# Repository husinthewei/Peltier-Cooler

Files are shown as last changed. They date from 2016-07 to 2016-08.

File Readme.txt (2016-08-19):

Peltier Cooler Project

Main Programs:
*FLoop: 
	-Arduino program. Found within the "Arduino Programs" directory. 
	-Controls the Peltier's, monitors temperature, and communicates with the python script.
	-Loaded onto Arduino. Does not have to be uploaded every use.

*Com.py: 
	-Python Script. Found within the "Python Scripts" directory
	-Reads the temperature outputs from the Arduino, logs them in files, and emails if there is failure
	-Must be ran every use

How to run Com.py(NOTE: CURRENTLY ON WORKS ON WINDOWS):
  Requirements-
	*python:
	  There are many options to install python. There are tutorials for Windows if googled, or you could download Enthought Canopy.
	*pip:
	  Download http://www.pip-installer.org/en/latest/installing.html
	  In cmd, cd to the directory of the file downloaded and type: python get-pip.py
	*pyserial:
	  After pip is installed, type in cmd: python -m pip install pyserial
	*pyqtgraph
	  After pip is installed, type in cmd: python -m pip install pyqtgraph
  Procedure 1 (command line)-
	1. cd to the directory of the python script. Ex: cd C:\Users\Your_Username\Documents\Github\Peltier-Cooler\PythonScripts
	2. type: python -B Com.py
	3. Enter the com port. Ex: Usually type: 0 
	4. Enter how often you want data output

  Procedure 2 (user interface)-
	1. go to the Pelter-Cooler folder
	2. double click: RunPython
	3. Enter the com port. Ex: Usually type: 0 
	4. Enter how often you want data output

How to run FLoop:
  Requirements-
	*Arduino IDE:
	  https://www.arduino.cc/en/Main/Software
  Procedure-
	1. The Arduino program is likely already on the board. It automatically starts running when the Arduino is turned on.
	2. If not loaded on, run the Arduino IDE and open FLoop
	3. Click the upload button on the top left

Where to find data outputs: 
	- The data outputs are in a folder called "Logs" inside the PythonScripts directory
	- They are in the form of csv files and include a timestamp in their names. 
	
*NOTE: There are heavily commented versions of the programs left in the folders
*These may be used for better understanding of the programs
*However, they are likely obsolete and should not be run
*The other files/programs are either irrelevant or tests

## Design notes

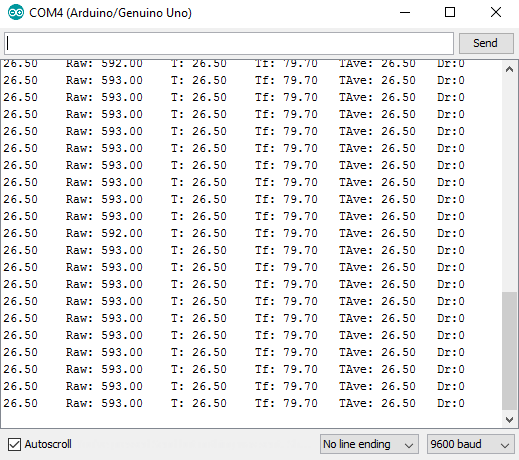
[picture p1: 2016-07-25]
PythonScripts/Images/arduinoOut.png

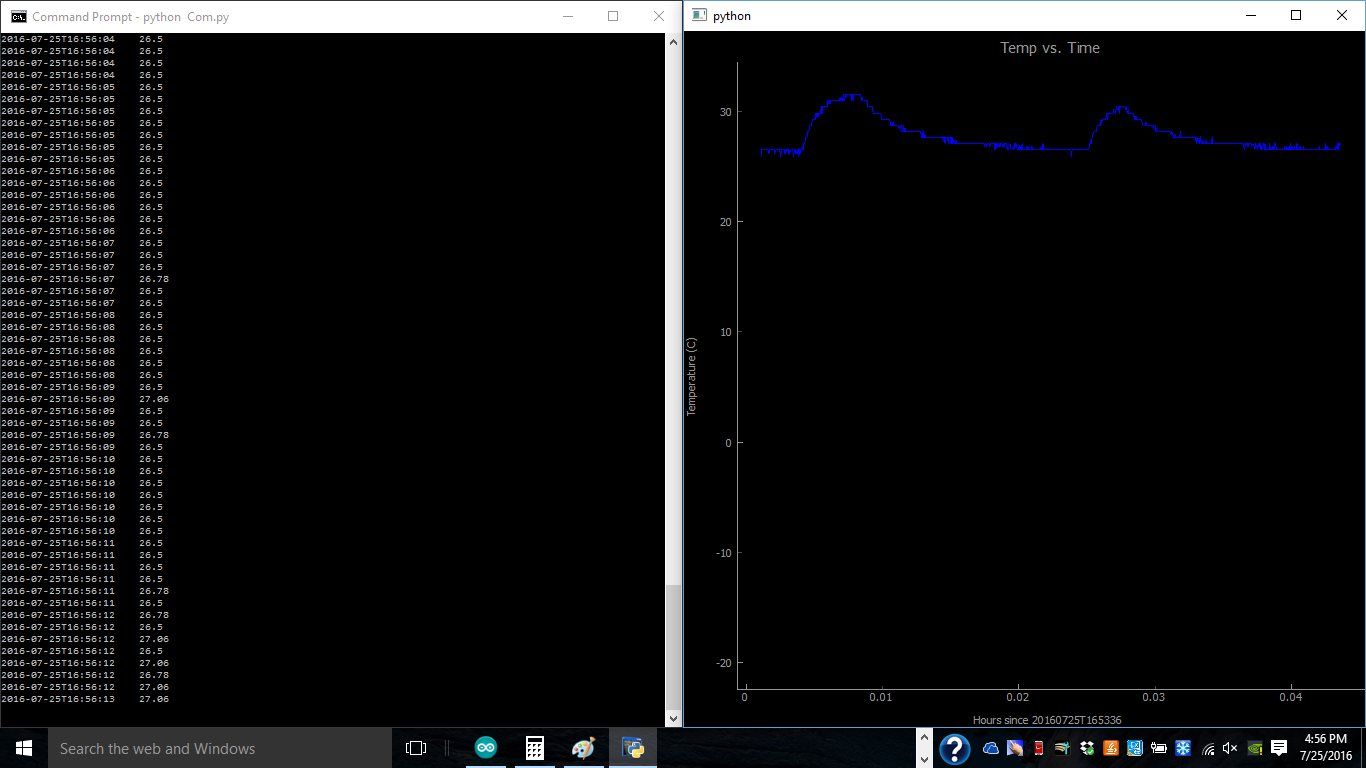
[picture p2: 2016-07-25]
PythonScripts/Images/GraphAndTerminal.png

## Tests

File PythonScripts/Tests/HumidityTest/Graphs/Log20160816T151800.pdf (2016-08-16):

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

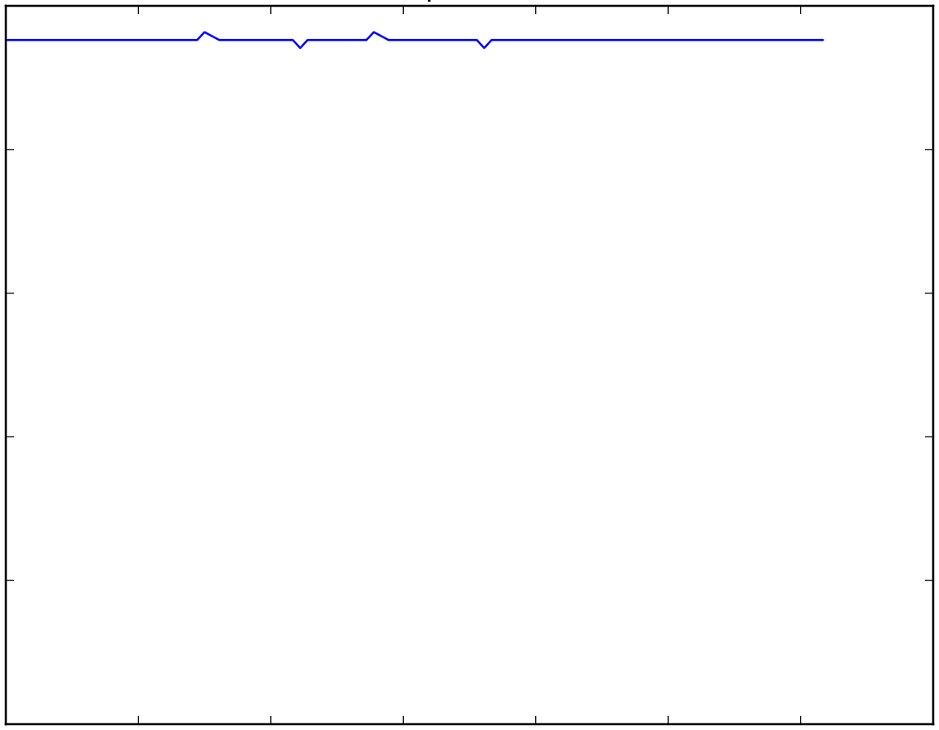
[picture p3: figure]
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

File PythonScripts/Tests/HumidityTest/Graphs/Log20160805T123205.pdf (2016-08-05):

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

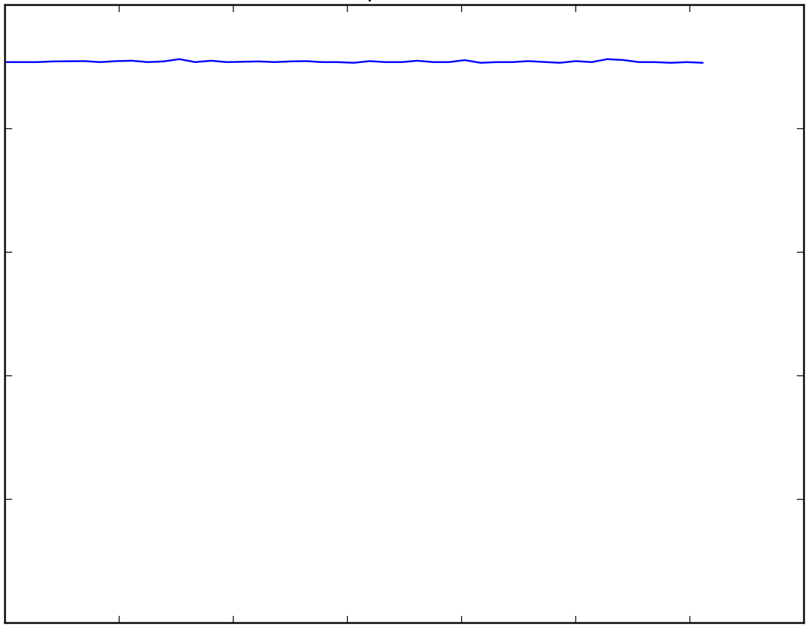
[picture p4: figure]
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

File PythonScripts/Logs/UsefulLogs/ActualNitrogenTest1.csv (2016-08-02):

2016-08-01T10:28:55 | -9.62905263158
2016-08-01T10:29:05 | -9.86350515464
2016-08-01T10:29:15 | -10.2303157895
2016-08-01T10:29:25 | -10.395106383
2016-08-01T10:29:36 | -10.7461702128
2016-08-01T10:29:46 | -10.9457446809
2016-08-01T10:29:56 | -11.1125531915
2016-08-01T10:30:06 | -11.4163829787
2016-08-01T10:30:16 | -11.5117021277
2016-08-01T10:30:26 | -11.5891489362
2016-08-01T10:30:36 | -11.7738297872
2016-08-01T10:30:46 | -11.9585106383
2016-08-01T10:30:56 | -12.0061702128
2016-08-01T10:31:06 | -12.0776595745
2016-08-01T10:31:16 | -12.2009473684
2016-08-01T10:31:26 | -12.3188421053
2016-08-01T10:31:36 | -12.4838947368
2016-08-01T10:31:46 | -12.5428421053
2016-08-01T10:31:56 | -12.5605263158
2016-08-01T10:32:06 | -12.6135789474
2016-08-01T10:32:16 | -12.6312631579
2016-08-01T10:32:26 | -12.6902105263
2016-08-01T10:32:36 | -12.7727368421
2016-08-01T10:32:46 | -12.8493684211
2016-08-01T10:32:56 | -12.8729473684
2016-08-01T10:33:06 | -12.8729473684
2016-08-01T10:33:16 | -13.0203157895
2016-08-01T10:33:26 | -13.1087368421
2016-08-01T10:33:36 | -13.15
2016-08-01T10:33:47 | -13.1323157895
2016-08-01T10:33:57 | -13.1558947368
2016-08-01T10:34:07 | -13.1912631579
2016-08-01T10:34:17 | -13.1971578947
2016-08-01T10:34:27 | -13.2266315789
2016-08-01T10:34:37 | -13.2914736842
2016-08-01T10:34:47 | -13.3091578947
2016-08-01T10:34:57 | -13.4034736842
2016-08-01T10:35:07 | -13.4801052632
2016-08-01T10:35:17 | -13.4683157895
2016-08-01T10:35:27 | -13.6213684211
2016-08-01T10:35:37 | -13.6274736842
2016-08-01T10:35:47 | -13.6745263158
2016-08-01T10:35:57 | -13.6509473684
2016-08-01T10:36:07 | -13.6628421053
2016-08-01T10:36:17 | -13.6391578947
2016-08-01T10:36:27 | -13.6510526316
2016-08-01T10:36:37 | -13.6982105263
2016-08-01T10:36:47 | -13.7272631579
2016-08-01T10:36:57 | -13.7038947368
2016-08-01T10:37:07 | -13.7211578947
2016-08-01T10:37:17 | -13.7036842105
2016-08-01T10:37:27 | -13.7094736842
2016-08-01T10:37:37 | -13.7210526316
2016-08-01T10:37:47 | -13.7272631579
2016-08-01T10:37:57 | -13.7561052632
2016-08-01T10:38:08 | -13.7736842105
2016-08-01T10:38:18 | -13.7910526316
2016-08-01T10:38:28 | -13.7968421053
2016-08-01T10:38:38 | -13.8025263158
2016-08-01T10:38:48 | -13.8316842105
2016-08-01T10:38:58 | -13.9185263158
2016-08-01T10:39:08 | -13.9243157895
2016-08-01T10:39:18 | -13.9414736842
2016-08-01T10:39:28 | -13.9994736842
2016-08-01T10:39:38 | -13.9937894737
2016-08-01T10:39:48 | -14.0458947368
2016-08-01T10:39:58 | -14.0051578947
2016-08-01T10:40:08 | -14.0109473684
2016-08-01T10:40:18 | -13.9937894737
2016-08-01T10:40:28 | -14.0515789474
2016-08-01T10:40:38 | -14.0401052632
2016-08-01T10:40:48 | -14.0918947368
2016-08-01T10:40:58 | -14.0921052632
2016-08-01T10:41:08 | -14.1327368421
2016-08-01T10:41:18 | -14.1498947368
2016-08-01T10:41:28 | -14.1329473684
2016-08-01T10:41:38 | -14.1327368421
2016-08-01T10:41:48 | -14.0747368421
2016-08-01T10:41:58 | -14.1212631579
2016-08-01T10:42:08 | -14.1152631579
2016-08-01T10:42:18 | -14.1501052632
2016-08-01T10:42:28 | -14.1796842105
2016-08-01T10:42:39 | -14.1616842105
2016-08-01T10:42:49 | -14.1672631579
2016-08-01T10:42:59 | -14.1326315789
2016-08-01T10:43:09 | -14.1849473684
2016-08-01T10:43:19 | -14.1731578947
2016-08-01T10:43:29 | -14.1554736842
2016-08-01T10:43:39 | -14.1441052632
2016-08-01T10:43:49 | -14.1968421053
2016-08-01T10:43:59 | -14.1443157895
2016-08-01T10:44:09 | -14.1906315789
2016-08-01T10:44:19 | -14.1674736842
2016-08-01T10:44:29 | -14.1965263158
2016-08-01T10:44:39 | -14.2255789474
2016-08-01T10:44:49 | -14.1791578947
2016-08-01T10:44:59 | -14.2083157895
2016-08-01T10:45:09 | -14.1675789474
2016-08-01T10:45:19 | -14.1556842105
2016-08-01T10:45:29 | -14.1615789474
2016-08-01T10:45:39 | -13.9529473684
2016-08-01T10:45:49 | -13.8314736842
2016-08-01T10:45:59 | -13.878
2016-08-01T10:46:09 | -13.9067368421
2016-08-01T10:46:19 | -14.0283157895
2016-08-01T10:46:29 | -14.0748421053
2016-08-01T10:46:39 | -14.0748421053
2016-08-01T10:46:49 | -14.1094736842
2016-08-01T10:47:00 | -14.1498947368
2016-08-01T10:47:10 | -14.1382105263
2016-08-01T10:47:20 | -14.1443157895
2016-08-01T10:47:30 | -14.2024210526
2016-08-01T10:47:40 | -14.1849473684
2016-08-01T10:47:50 | -14.1733684211
2016-08-01T10:48:00 | -14.2197894737
2016-08-01T10:48:10 | -14.1732631579
2016-08-01T10:48:20 | -14.2078947368
2016-08-01T10:48:30 | -14.2254736842
2016-08-01T10:48:40 | -14.2604210526
2016-08-01T10:48:50 | -14.2606315789
2016-08-01T10:49:00 | -14.2663157895
2016-08-01T10:49:10 | -14.2721052632
2016-08-01T10:49:20 | -14.2313684211
2016-08-01T10:49:30 | -14.2429473684
2016-08-01T10:49:40 | -14.2546315789
2016-08-01T10:49:50 | -14.2197894737
2016-08-01T10:50:00 | -14.2255789474
2016-08-01T10:50:10 | -14.2544210526
2016-08-01T10:50:20 | -14.272
2016-08-01T10:50:30 | -14.2837894737
2016-08-01T10:50:40 | -14.2663157895
2016-08-01T10:50:50 | -14.2662105263
2016-08-01T10:51:00 | -14.2605263158
2016-08-01T10:51:10 | -14.2428421053
2016-08-01T10:51:21 | -14.2781052632
2016-08-01T10:51:31 | -14.2428421053
2016-08-01T10:51:41 | -14.1849473684
2016-08-01T10:51:51 | -14.0630526316
2016-08-01T10:52:01 | -14.0575789474
2016-08-01T10:52:11 | -14.0344210526
2016-08-01T10:52:21 | -14.0922105263
2016-08-01T10:52:31 | -14.0746315789
2016-08-01T10:52:41 | -14.1269473684
2016-08-01T10:52:51 | -14.1269473684
2016-08-01T10:53:01 | -14.1384210526
2016-08-01T10:53:11 | -14.1616842105
2016-08-01T10:53:21 | -14.156
2016-08-01T10:53:31 | -14.1907368421
2016-08-01T10:53:41 | -14.1965263158
2016-08-01T10:53:51 | -14.2023157895
2016-08-01T10:54:01 | -14.1849473684
2016-08-01T10:54:11 | -14.1731578947
2016-08-01T10:54:21 | -14.1965263158
2016-08-01T10:54:31 | -14.1502105263
2016-08-01T10:54:41 | -14.1271578947
2016-08-01T10:54:51 | -14.1268421053
2016-08-01T10:55:01 | -14.1617894737
2016-08-01T10:55:11 | -14.1269473684
2016-08-01T10:55:21 | -14.1673684211
2016-08-01T10:55:31 | -14.1502105263
2016-08-01T10:55:41 | -14.2025263158
2016-08-01T10:55:52 | -14.2025263158
2016-08-01T10:56:02 | -14.2316842105
2016-08-01T10:56:12 | -14.1904210526
2016-08-01T10:56:22 | -14.2196842105
2016-08-01T10:56:32 | -14.1965263158
2016-08-01T10:56:42 | -14.2370526316
2016-08-01T10:56:52 | -14.2431578947
2016-08-01T10:57:02 | -14.1790526316
2016-08-01T10:57:12 | -14.2429473684
2016-08-01T10:57:22 | -14.2023157895
2016-08-01T10:57:32 | -14.2196842105
2016-08-01T10:57:42 | -14.1967368421
2016-08-01T10:57:52 | -14.208
2016-08-01T10:58:02 | -14.1674736842
2016-08-01T10:58:12 | -14.226
2016-08-01T10:58:22 | -14.2081052632
2016-08-01T10:58:32 | -14.2257894737
2016-08-01T10:58:42 | -14.2082105263
2016-08-01T10:58:52 | -14.1673684211
2016-08-01T10:59:02 | -14.1849473684
2016-08-01T10:59:12 | -14.1384210526
2016-08-01T10:59:22 | -14.0690526316
2016-08-01T10:59:32 | -13.8835789474
2016-08-01T10:59:42 | -13.8836842105
2016-08-01T10:59:52 | -13.93
2016-08-01T11:00:02 | -13.9009473684
2016-08-01T11:00:13 | -13.9706315789
2016-08-01T11:00:23 | -13.9704210526
2016-08-01T11:00:33 | -14.0285263158
2016-08-01T11:00:43 | -14.0226315789
2016-08-01T11:00:53 | -14.0053684211
2016-08-01T11:01:03 | -14.0401052632
2016-08-01T11:01:13 | -14.0631578947
2016-08-01T11:01:23 | -14.0807368421
2016-08-01T11:01:33 | -14.0867368421
2016-08-01T11:01:43 | -14.1211578947
2016-08-01T11:01:53 | -14.0981052632
2016-08-01T11:02:03 | -14.0341052632
2016-08-01T11:02:13 | -14.1096842105
2016-08-01T11:02:23 | -14.0976842105
2016-08-01T11:02:33 | -14.1498947368
2016-08-01T11:02:43 | -14.1269473684
2016-08-01T11:02:53 | -14.0982105263
2016-08-01T11:03:03 | -14.1502105263
2016-08-01T11:03:13 | -14.1384210526
2016-08-01T11:03:23 | -14.15
2016-08-01T11:03:33 | -14.1269473684
2016-08-01T11:03:43 | -14.1561052632
2016-08-01T11:03:53 | -14.1211578947
2016-08-01T11:04:03 | -14.1094736842
2016-08-01T11:04:13 | -14.1965263158
2016-08-01T11:04:23 | -14.15
2016-08-01T11:04:34 | -14.1672631579
2016-08-01T11:04:44 | -14.1615789474
2016-08-01T11:04:54 | -14.1675789474
2016-08-01T11:05:04 | -14.2024210526
2016-08-01T11:05:14 | -14.1675789474
2016-08-01T11:05:24 | -14.1907368421
2016-08-01T11:05:34 | -14.1790526316
2016-08-01T11:05:44 | -14.1443157895
2016-08-01T11:05:54 | -14.1445263158
2016-08-01T11:06:04 | -14.1733684211
2016-08-01T11:06:14 | -14.1734736842
2016-08-01T11:06:24 | -14.1848421053
2016-08-01T11:06:34 | -14.1963157895
2016-08-01T11:06:44 | -14.2315789474
2016-08-01T11:06:54 | -14.1730526316
2016-08-01T11:07:04 | -14.1963157895
2016-08-01T11:07:14 | -14.2021052632
2016-08-01T11:07:24 | -14.2255789474
2016-08-01T11:07:34 | -14.2372631579
2016-08-01T11:07:44 | -14.2196842105
2016-08-01T11:07:54 | -14.2254736842
2016-08-01T11:08:04 | -14.2082105263
2016-08-01T11:08:14 | -14.2372631579
2016-08-01T11:08:24 | -14.2431578947
2016-08-01T11:08:34 | -14.2137894737
2016-08-01T11:08:44 | -14.2195789474
2016-08-01T11:08:54 | -14.2371578947
2016-08-01T11:09:05 | -14.2548421053
2016-08-01T11:09:15 | -14.1907368421
2016-08-01T11:09:25 | -14.1213684211
2016-08-01T11:09:35 | -14.226
2016-08-01T11:09:45 | -14.1907368421
2016-08-01T11:09:55 | -14.2023157895
2016-08-01T11:10:05 | -14.208
2016-08-01T11:10:15 | -14.1675789474
2016-08-01T11:10:25 | -14.1617894737
2016-08-01T11:10:35 | -14.0224210526
2016-08-01T11:10:45 | -14.1093684211
2016-08-01T11:10:55 | -14.1905263158
2016-08-01T11:11:05 | -14.1616842105
2016-08-01T11:11:15 | -14.2605263158
2016-08-01T11:11:25 | -14.2256842105
2016-08-01T11:11:35 | -14.2430526316
2016-08-01T11:11:45 | -14.2255789474
2016-08-01T11:11:55 | -14.2372631579
2016-08-01T11:12:05 | -14.2490526316
2016-08-01T11:12:15 | -14.2606315789
2016-08-01T11:12:25 | -14.2313684211
2016-08-01T11:12:35 | -14.2314736842
2016-08-01T11:12:45 | -14.2661052632
2016-08-01T11:12:55 | -14.2662105263
2016-08-01T11:13:05 | -14.2136842105
2016-08-01T11:13:15 | -14.2549473684
2016-08-01T11:13:26 | -14.2197894737
2016-08-01T11:13:36 | -14.2312631579
2016-08-01T11:13:46 | -14.1964210526
2016-08-01T11:13:56 | -14.1851578947
2016-08-01T11:14:06 | -14.1789473684
2016-08-01T11:14:16 | -14.1966315789
2016-08-01T11:14:26 | -14.2254736842
2016-08-01T11:14:36 | -14.2313684211
2016-08-01T11:14:46 | -14.22
2016-08-01T11:14:56 | -14.1906315789
2016-08-01T11:15:06 | -14.2661052632
2016-08-01T11:15:16 | -14.214
2016-08-01T11:15:26 | -14.2022105263
2016-08-01T11:15:36 | -14.2024210526
2016-08-01T11:15:46 | -14.1963157895
2016-08-01T11:15:56 | -14.2195789474
2016-08-01T11:16:06 | -14.2198947368
2016-08-01T11:16:16 | -14.2313684211
2016-08-01T11:16:26 | -14.2428421053
2016-08-01T11:16:36 | -14.2724210526
2016-08-01T11:16:46 | -14.2257894737
2016-08-01T11:16:56 | -14.2312631579
2016-08-01T11:17:06 | -14.2314736842
2016-08-01T11:17:16 | -14.2313684211
2016-08-01T11:17:26 | -14.2082105263
2016-08-01T11:17:36 | -14.2430526316
2016-08-01T11:17:47 | -14.2081052632
2016-08-01T11:17:57 | -14.1673684211
2016-08-01T11:18:07 | -14.2428421053
2016-08-01T11:18:17 | -14.1847368421
2016-08-01T11:18:27 | -14.2083157895
2016-08-01T11:18:37 | -14.2723157895
2016-08-01T11:18:47 | -14.208
2016-08-01T11:18:57 | -14.2429473684
2016-08-01T11:19:07 | -14.2311578947
2016-08-01T11:19:17 | -14.2371578947
2016-08-01T11:19:27 | -14.3076842105
2016-08-01T11:19:37 | -14.2604210526
2016-08-01T11:19:47 | -14.2254736842
2016-08-01T11:19:57 | -14.2371578947
2016-08-01T11:20:07 | -14.2431578947
2016-08-01T11:20:17 | -14.2549473684
2016-08-01T11:20:27 | -14.2257894737
2016-08-01T11:20:37 | -14.22
2016-08-01T11:20:47 | -14.2489473684
2016-08-01T11:20:57 | -14.2314736842
2016-08-01T11:21:07 | -14.2314736842
2016-08-01T11:21:17 | -14.214
2016-08-01T11:21:27 | -14.2369473684
2016-08-01T11:21:37 | -14.2137894737
2016-08-01T11:21:47 | -14.2431578947
2016-08-01T11:21:57 | -14.2255789474
2016-08-01T11:22:07 | -14.2315789474
2016-08-01T11:22:18 | -14.2194736842
2016-08-01T11:22:28 | -14.2082105263
2016-08-01T11:22:38 | -14.2486315789
2016-08-01T11:22:48 | -14.2901052632
2016-08-01T11:22:58 | -14.2487368421
2016-08-01T11:23:08 | -14.2842105263
2016-08-01T11:23:18 | -14.2896842105
2016-08-01T11:23:28 | -14.2837894737
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

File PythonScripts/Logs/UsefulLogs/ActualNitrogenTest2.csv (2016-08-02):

2016-08-01T14:31:42 | 26.0692307692
2016-08-01T14:31:52 | 26.0092783505
2016-08-01T14:32:03 | 26.0092783505
2016-08-01T14:32:13 | 24.0405154639
2016-08-01T14:32:23 | 17.8235051546
2016-08-01T14:32:33 | 11.6530927835
2016-08-01T14:32:43 | 7.15367346939
2016-08-01T14:32:53 | 3.84326530612
2016-08-01T14:33:03 | 1.46153061224
2016-08-01T14:33:13 | -0.165360824742
2016-08-01T14:33:23 | -1.46041237113
2016-08-01T14:33:33 | -2.55731958763
2016-08-01T14:33:43 | -3.43453608247
2016-08-01T14:33:53 | -4.19278350515
2016-08-01T14:34:03 | -4.85659793814
2016-08-01T14:34:13 | -5.43969072165
2016-08-01T14:34:23 | -5.97659793814
2016-08-01T14:34:33 | -6.45
2016-08-01T14:34:43 | -6.80216494845
2016-08-01T14:34:53 | -7.12896907216
2016-08-01T14:35:04 | -7.50958762887
2016-08-01T14:35:14 | -7.66422680412
2016-08-01T14:35:24 | -7.94103092784
2016-08-01T14:35:34 | -7.99886597938
2016-08-01T14:35:44 | -8.18927835052
2016-08-01T14:35:54 | -8.40865979381
2016-08-01T14:36:04 | -8.63381443299
2016-08-01T14:36:14 | -8.72041237113
2016-08-01T14:36:24 | -8.83010309278
2016-08-01T14:36:34 | -8.98597938144
2016-08-01T14:36:44 | -9.18216494845
2016-08-01T14:36:54 | -9.28618556701
2016-08-01T14:37:04 | -9.40742268041
2016-08-01T14:37:14 | -9.44206185567
2016-08-01T14:37:24 | -9.48824742268
2016-08-01T14:37:34 | -9.47670103093
2016-08-01T14:37:44 | -9.50556701031
2016-08-01T14:37:54 | -9.44206185567
2016-08-01T14:38:04 | -9.45360824742
2016-08-01T14:38:14 | -9.37855670103
2016-08-01T14:38:24 | -9.25731958763
2016-08-01T14:38:35 | -9.17649484536
2016-08-01T14:38:45 | -9.17639175258
2016-08-01T14:38:55 | -9.17072164948
2016-08-01T14:39:05 | -9.17072164948
2016-08-01T14:39:15 | -9.16494845361
2016-08-01T14:39:25 | -9.20525773196
2016-08-01T14:39:35 | -9.21113402062
2016-08-01T14:39:45 | -9.25154639175
2016-08-01T14:39:55 | -9.32082474227
2016-08-01T14:40:05 | -9.3381443299
2016-08-01T14:40:15 | -9.35546391753
2016-08-01T14:40:25 | -9.37855670103
2016-08-01T14:40:35 | -9.39577319588
2016-08-01T14:40:45 | -9.3612371134
2016-08-01T14:40:55 | -9.42474226804
2016-08-01T14:41:05 | -9.43628865979
2016-08-01T14:41:15 | -9.44206185567
2016-08-01T14:41:25 | -9.41896907216
2016-08-01T14:41:35 | -9.37855670103
2016-08-01T14:41:45 | -9.49402061856
2016-08-01T14:41:56 | -9.44206185567
2016-08-01T14:42:06 | -9.52865979381
2016-08-01T14:42:16 | -9.61525773196
2016-08-01T14:42:26 | -9.67865979381
2016-08-01T14:42:36 | -9.7075257732
2016-08-01T14:42:46 | -9.74804123711
2016-08-01T14:42:56 | -9.74226804124
2016-08-01T14:43:06 | -9.77690721649
2016-08-01T14:43:16 | -9.73072164948
2016-08-01T14:43:26 | -9.7824742268
2016-08-01T14:43:36 | -9.74226804124
2016-08-01T14:43:46 | -9.75958762887
2016-08-01T14:43:56 | -9.80577319588
2016-08-01T14:44:06 | -9.75381443299
2016-08-01T14:44:16 | -9.80556701031
2016-08-01T14:44:26 | -9.84608247423
2016-08-01T14:44:36 | -9.78257731959
2016-08-01T14:44:46 | -9.8287628866
2016-08-01T14:44:57 | -9.83463917526
2016-08-01T14:45:07 | -9.89804123711
2016-08-01T14:45:17 | -9.87484536082
2016-08-01T14:45:27 | -9.90969072165
2016-08-01T14:45:37 | -9.88639175258
2016-08-01T14:45:47 | -9.95145833333
2016-08-01T14:45:57 | -9.90489583333
2016-08-01T14:46:07 | -9.9340625
2016-08-01T14:46:17 | -9.86340206186
2016-08-01T14:46:27 | -9.92229166667
2016-08-01T14:46:37 | -9.92822916667
2016-08-01T14:46:47 | -9.905
2016-08-01T14:46:57 | -9.9340625
2016-08-01T14:47:07 | -9.92802083333
2016-08-01T14:47:17 | -9.87505154639
2016-08-01T14:47:27 | -9.81154639175
2016-08-01T14:47:37 | -9.82309278351
2016-08-01T14:47:47 | -9.8518556701
2016-08-01T14:47:57 | -9.83463917526
2016-08-01T14:48:07 | -9.91072916667
2016-08-01T14:48:18 | -9.88639175258
2016-08-01T14:48:28 | -9.9212371134
2016-08-01T14:48:38 | -9.9340625
2016-08-01T14:48:48 | -9.96895833333
2016-08-01T14:48:58 | -10.0041666667
2016-08-01T14:49:08 | -9.98666666667
2016-08-01T14:49:18 | -9.98083333333
2016-08-01T14:49:28 | -10.0215625
2016-08-01T14:49:38 | -10.0332291667
2016-08-01T14:49:48 | -10.0768421053
2016-08-01T14:49:58 | -10.0040625
2016-08-01T14:50:08 | -10.0157291667
2016-08-01T14:50:18 | -10.0298947368
2016-08-01T14:50:28 | -10.0391666667
2016-08-01T14:50:38 | -10.1475789474
2016-08-01T14:50:48 | -10.1536842105
2016-08-01T14:50:58 | -10.1418947368
2016-08-01T14:51:09 | -10.2184210526
2016-08-01T14:51:19 | -10.2244210526
2016-08-01T14:51:29 | -10.3062765957
2016-08-01T14:51:39 | -10.330106383
2016-08-01T14:51:49 | -10.3181914894
2016-08-01T14:51:59 | -10.330106383
2016-08-01T14:52:09 | -10.329787234
2016-08-01T14:52:19 | -10.2947368421
2016-08-01T14:52:29 | -10.3179787234
2016-08-01T14:52:39 | -10.3179787234
2016-08-01T14:52:49 | -10.3654255319
2016-08-01T14:52:59 | -10.3479787234
2016-08-01T14:53:09 | -10.2948421053
2016-08-01T14:53:19 | -10.1769473684
2016-08-01T14:53:29 | -10.1653684211
2016-08-01T14:53:39 | -10.2596842105
2016-08-01T14:53:49 | -10.2822340426
2016-08-01T14:53:59 | -10.2714736842
2016-08-01T14:54:09 | -10.3121276596
2016-08-01T14:54:19 | -10.3180851064
2016-08-01T14:54:29 | -10.3061702128
2016-08-01T14:54:39 | -10.330106383
2016-08-01T14:54:49 | -10.3594680851
2016-08-01T14:54:59 | -10.3594680851
2016-08-01T14:55:09 | -10.394893617
2016-08-01T14:55:19 | -10.3594680851
2016-08-01T14:55:29 | -10.3657446809
2016-08-01T14:55:40 | -10.3654255319
2016-08-01T14:55:50 | -10.3420212766
2016-08-01T14:56:00 | -10.3653191489
2016-08-01T14:56:10 | -10.3061702128
2016-08-01T14:56:20 | -10.3121276596
2016-08-01T14:56:30 | -10.3358510638
2016-08-01T14:56:40 | -10.3064210526
2016-08-01T14:56:50 | -10.3240425532
2016-08-01T14:57:00 | -10.3180851064
2016-08-01T14:57:10 | -10.2949473684
2016-08-01T14:57:20 | -10.2891578947
2016-08-01T14:57:30 | -10.2942553191
2016-08-01T14:57:40 | -10.33
2016-08-01T14:57:50 | -10.2302105263
2016-08-01T14:58:00 | -10.2417894737
2016-08-01T14:58:10 | -10.2593684211
2016-08-01T14:58:20 | -10.2596842105
2016-08-01T14:58:30 | -10.3180851064
2016-08-01T14:58:40 | -10.2417894737
2016-08-01T14:58:50 | -10.3179787234
2016-08-01T14:59:01 | -10.2361052632
2016-08-01T14:59:11 | -10.1948421053
2016-08-01T14:59:21 | -10.2066315789
2016-08-01T14:59:31 | -10.2537894737
2016-08-01T14:59:41 | -10.2477894737
2016-08-01T14:59:51 | -10.2537894737
2016-08-01T15:00:01 | -10.2477894737
2016-08-01T15:00:11 | -10.2477894737
2016-08-01T15:00:21 | -10.33
2016-08-01T15:00:31 | -10.2882978723
2016-08-01T15:00:41 | -10.300212766
2016-08-01T15:00:51 | -10.3241489362
2016-08-01T15:01:01 | -10.2941489362
2016-08-01T15:01:11 | -10.3121276596
2016-08-01T15:01:21 | -10.3122340426
2016-08-01T15:01:31 | -10.3179787234
2016-08-01T15:01:41 | -10.2714736842
2016-08-01T15:01:51 | -10.2646808511
2016-08-01T15:02:01 | -10.2771578947
2016-08-01T15:02:12 | -10.2596842105
2016-08-01T15:02:22 | -10.2597894737
2016-08-01T15:02:32 | -10.2830526316
2016-08-01T15:02:42 | -10.329787234
2016-08-01T15:02:52 | -10.2890526316
2016-08-01T15:03:02 | -10.2706382979
2016-08-01T15:03:12 | -10.3237234043
2016-08-01T15:03:22 | -10.3654255319
2016-08-01T15:03:32 | -10.4713829787
2016-08-01T15:03:42 | -10.5763829787
2016-08-01T15:03:52 | -10.8280851064
2016-08-01T15:04:02 | -10.9756382979
2016-08-01T15:04:12 | -11.3272340426
2016-08-01T15:04:22 | -11.4880851064
2016-08-01T15:04:32 | -11.6428723404
2016-08-01T15:04:42 | -11.9763829787
2016-08-01T15:04:52 | -12.000212766
2016-08-01T15:05:02 | -11.9824468085
2016-08-01T15:05:12 | -11.5831914894
2016-08-01T15:05:22 | -12.0359574468
2016-08-01T15:05:32 | -12.2363157895
2016-08-01T15:05:42 | -12.4309473684
2016-08-01T15:05:52 | -12.3836842105
2016-08-01T15:06:03 | -12.4662105263
2016-08-01T15:06:13 | -12.5487368421
2016-08-01T15:06:23 | -12.6076842105
2016-08-01T15:06:33 | -12.5958947368
2016-08-01T15:06:43 | -12.6430526316
2016-08-01T15:06:53 | -12.6666315789
2016-08-01T15:07:03 | -12.6842105263
2016-08-01T15:07:13 | -12.7786315789
2016-08-01T15:07:23 | -12.7491578947
2016-08-01T15:07:33 | -12.8670526316
2016-08-01T15:07:43 | -12.9317894737
2016-08-01T15:07:53 | -12.9613684211
2016-08-01T15:08:03 | -13.0026315789
2016-08-01T15:08:13 | -13.0497894737
2016-08-01T15:08:23 | -13.0556842105
2016-08-01T15:08:33 | -13.1205263158
2016-08-01T15:08:43 | -13.1204210526
2016-08-01T15:08:53 | -13.1087368421
2016-08-01T15:09:03 | -13.1675789474
2016-08-01T15:09:13 | -13.1323157895
2016-08-01T15:09:23 | -13.2028421053
2016-08-01T15:09:33 | -13.1558947368
2016-08-01T15:09:43 | -13.1382105263
2016-08-01T15:09:53 | -13.15
2016-08-01T15:10:04 | -13.1441052632
2016-08-01T15:10:14 | -13.1615789474
2016-08-01T15:10:24 | -13.1790526316
2016-08-01T15:10:34 | -13.1498947368
2016-08-01T15:10:44 | -13.1558947368
2016-08-01T15:10:54 | -13.1264210526
2016-08-01T15:11:04 | -13.0674736842
2016-08-01T15:11:14 | -13.0262105263
2016-08-01T15:11:24 | -13.1026315789
2016-08-01T15:11:34 | -13.1027368421
2016-08-01T15:11:44 | -13.1616842105
2016-08-01T15:11:54 | -13.1382105263
2016-08-01T15:12:04 | -13.144
2016-08-01T15:12:14 | -13.1676842105
2016-08-01T15:12:24 | -13.1912631579
2016-08-01T15:12:34 | -13.2382105263
2016-08-01T15:12:44 | -13.1970526316
2016-08-01T15:12:54 | -13.2205263158
2016-08-01T15:13:04 | -13.2736842105
2016-08-01T15:13:14 | -13.2442105263
2016-08-01T15:13:24 | -13.2383157895
2016-08-01T15:13:34 | -13.2973684211
2016-08-01T15:13:44 | -13.2618947368
2016-08-01T15:13:54 | -13.3148421053
2016-08-01T15:14:04 | -13.3444210526
2016-08-01T15:14:14 | -13.3854736842
2016-08-01T15:14:25 | -13.368
2016-08-01T15:14:35 | -13.4150526316
2016-08-01T15:14:45 | -13.3504210526
2016-08-01T15:14:55 | -13.3504210526
2016-08-01T15:15:05 | -13.3443157895
2016-08-01T15:15:15 | -13.3798947368
2016-08-01T15:15:25 | -13.3267368421
2016-08-01T15:15:35 | -13.3738947368
2016-08-01T15:15:45 | -13.4034736842
2016-08-01T15:15:55 | -13.3268421053
2016-08-01T15:16:05 | -13.3973684211
2016-08-01T15:16:15 | -13.362
2016-08-01T15:16:25 | -13.4092631579
2016-08-01T15:16:35 | -13.4564210526
2016-08-01T15:16:45 | -13.4327368421
2016-08-01T15:16:55 | -13.4561052632
2016-08-01T15:17:05 | -13.4446315789
2016-08-01T15:17:15 | -13.4211578947
2016-08-01T15:17:25 | -13.4506315789
2016-08-01T15:17:35 | -13.4150526316
2016-08-01T15:17:45 | -13.4564210526
2016-08-01T15:17:55 | -13.5211578947
2016-08-01T15:18:05 | -13.5092631579
2016-08-01T15:18:15 | -13.4976842105
2016-08-01T15:18:25 | -13.4564210526
2016-08-01T15:18:35 | -13.4387368421
2016-08-01T15:18:46 | -13.4446315789
2016-08-01T15:18:56 | -13.5449473684
2016-08-01T15:19:06 | -13.4916842105
2016-08-01T15:19:16 | -13.5270526316
2016-08-01T15:19:26 | -13.5564210526
2016-08-01T15:19:36 | -13.4210526316
2016-08-01T15:19:46 | -13.4917894737
2016-08-01T15:19:56 | -13.486
2016-08-01T15:20:06 | -13.5271578947
2016-08-01T15:20:16 | -13.3916842105
2016-08-01T15:20:26 | -13.4447368421
2016-08-01T15:20:36 | -13.4502105263
2016-08-01T15:20:46 | -13.486
2016-08-01T15:20:56 | -13.4975789474
2016-08-01T15:21:06 | -13.5328421053
2016-08-01T15:21:16 | -13.6095789474
2016-08-01T15:21:26 | -13.5213684211
2016-08-01T15:21:36 | -13.5625263158
2016-08-01T15:21:46 | -13.5624210526
2016-08-01T15:21:56 | -13.5507368421
2016-08-01T15:22:06 | -13.5978947368
2016-08-01T15:22:16 | -13.5448421053
2016-08-01T15:22:26 | -13.6093684211
2016-08-01T15:22:36 | -13.6037894737
2016-08-01T15:22:46 | -13.5802105263
2016-08-01T15:22:56 | -13.598
2016-08-01T15:23:07 | -13.5684210526
2016-08-01T15:23:17 | -13.5331578947
2016-08-01T15:23:27 | -13.5272631579
2016-08-01T15:23:37 | -13.5682105263
2016-08-01T15:23:47 | -13.5861052632
2016-08-01T15:23:57 | -13.5975789474
2016-08-01T15:24:07 | -13.5449473684
2016-08-01T15:24:17 | -13.6272631579
2016-08-01T15:24:27 | -13.6332631579
2016-08-01T15:24:37 | -13.6391578947
2016-08-01T15:24:47 | -13.6155789474
2016-08-01T15:24:57 | -13.5802105263
2016-08-01T15:25:07 | -13.5978947368
2016-08-01T15:25:17 | -13.5803157895
2016-08-01T15:25:27 | -13.5862105263
2016-08-01T15:25:37 | -13.5272631579
2016-08-01T15:25:47 | -13.5684210526
2016-08-01T15:25:57 | -13.5862105263
2016-08-01T15:26:07 | -13.5977894737
2016-08-01T15:26:17 | -13.5567368421
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

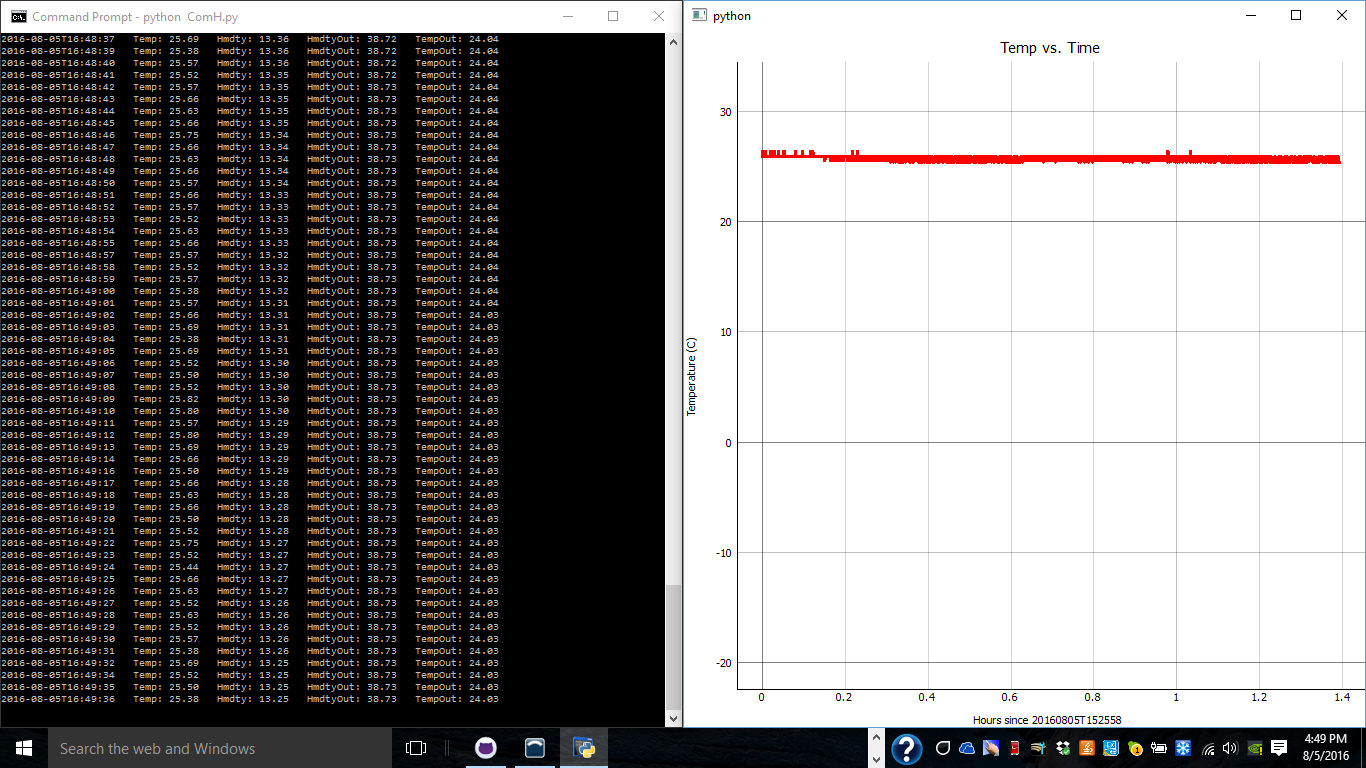
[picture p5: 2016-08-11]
PythonScripts/Images/FinalHumidityResults.png

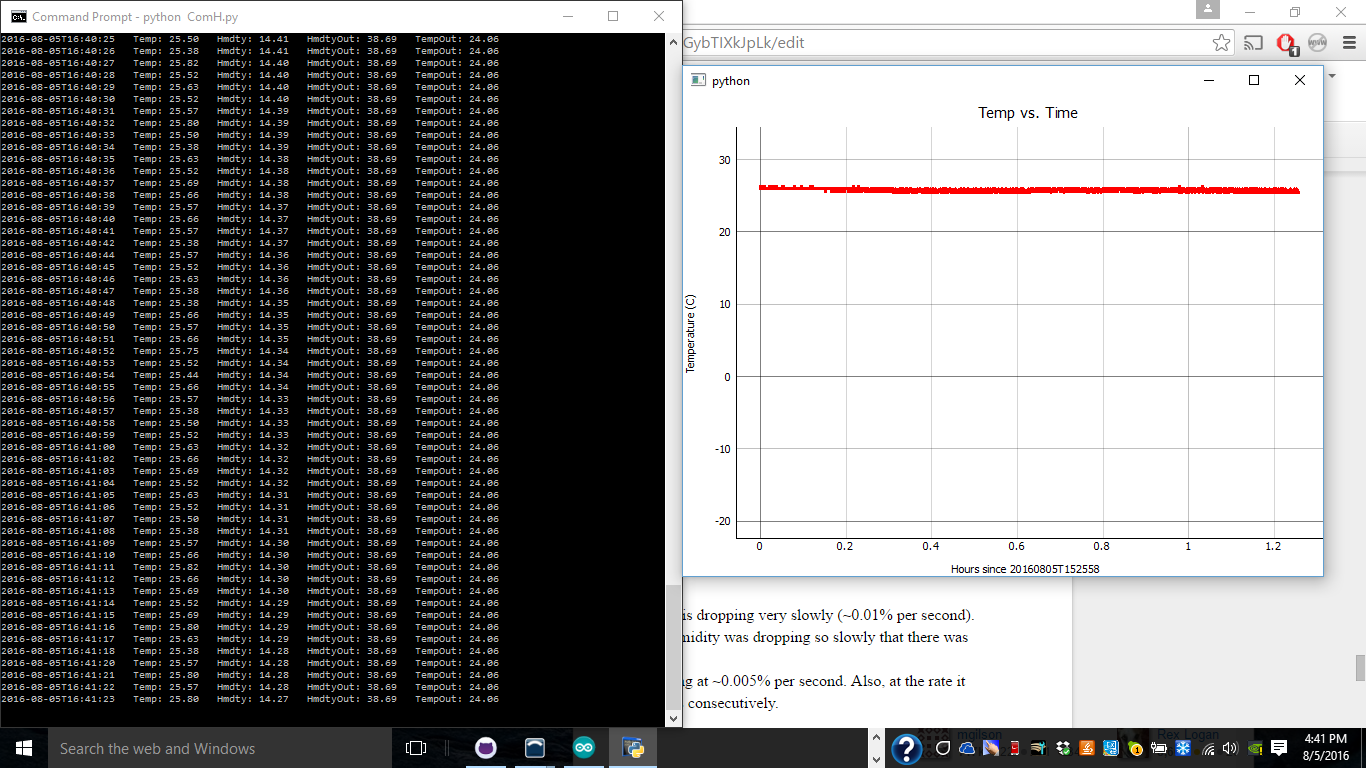
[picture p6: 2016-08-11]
PythonScripts/Images/HumidityResults.png

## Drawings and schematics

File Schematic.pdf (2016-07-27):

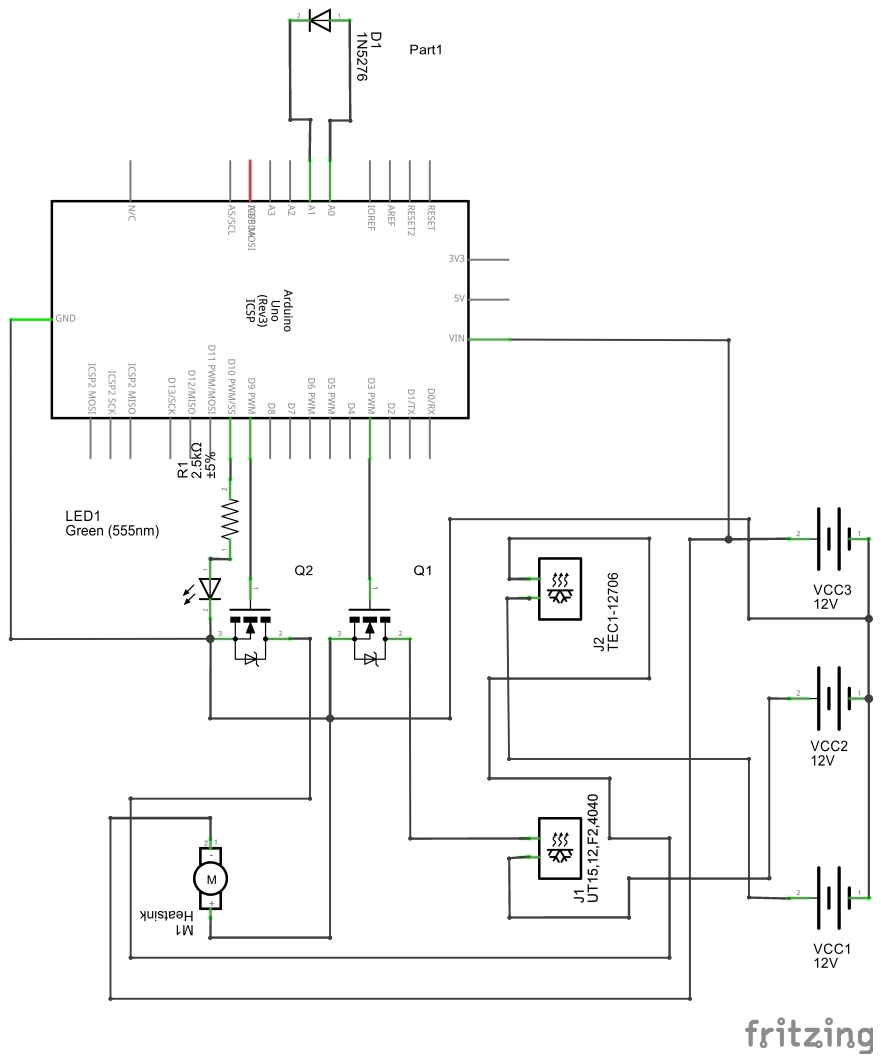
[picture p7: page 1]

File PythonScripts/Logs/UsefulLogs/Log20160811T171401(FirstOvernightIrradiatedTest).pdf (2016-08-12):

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

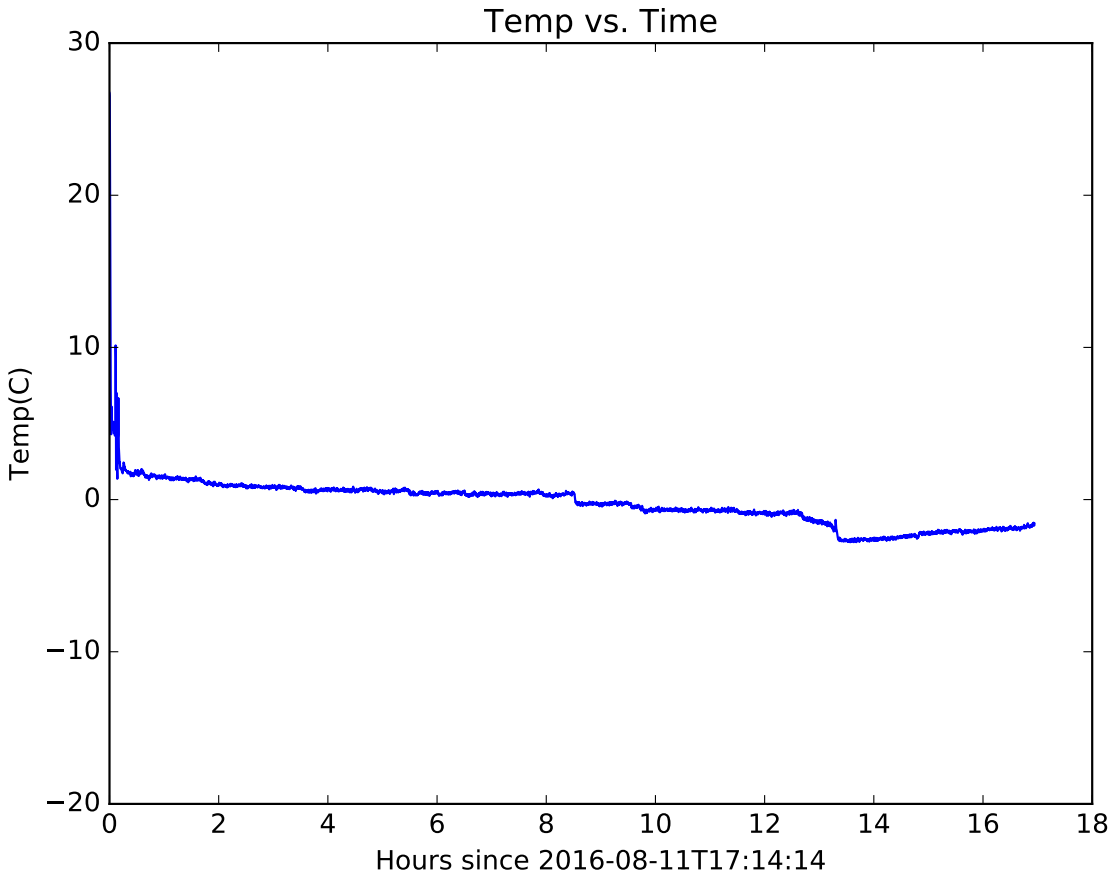
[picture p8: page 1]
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

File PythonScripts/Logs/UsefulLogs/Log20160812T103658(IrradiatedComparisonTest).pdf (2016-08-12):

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

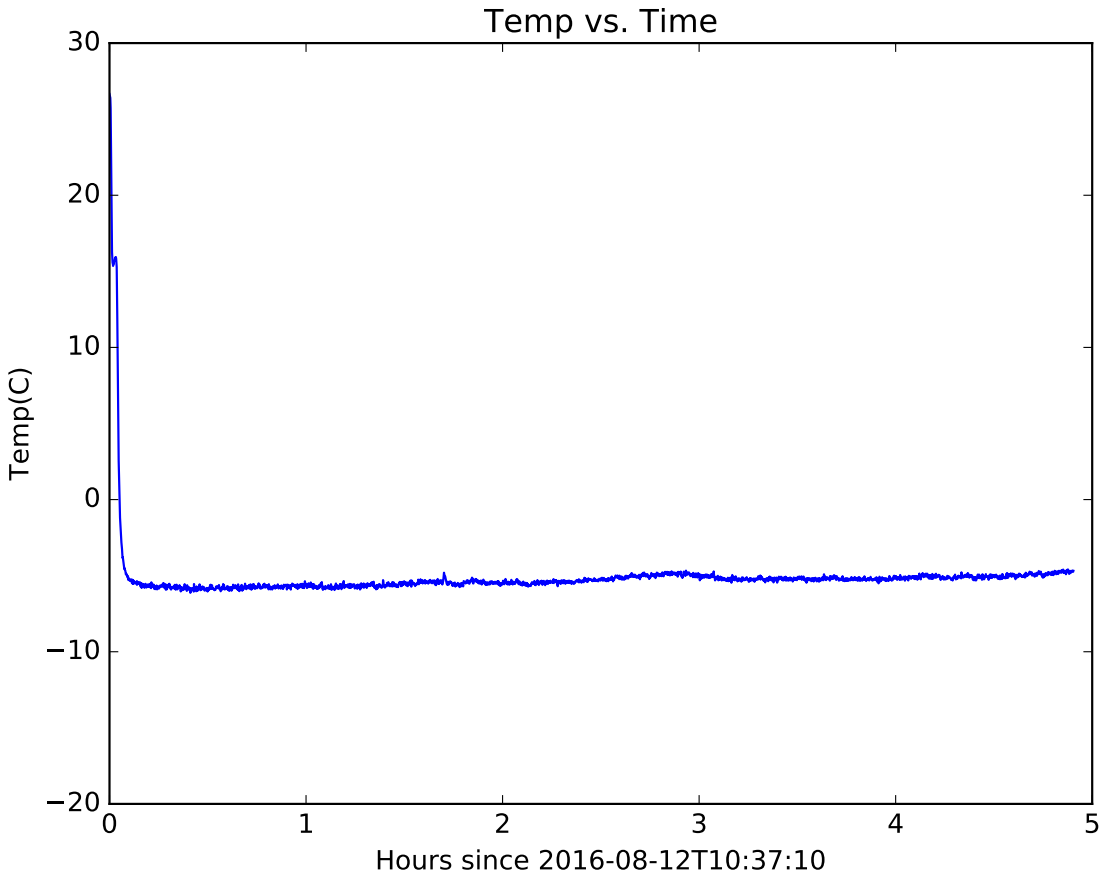
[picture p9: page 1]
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

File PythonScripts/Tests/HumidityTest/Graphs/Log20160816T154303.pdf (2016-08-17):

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

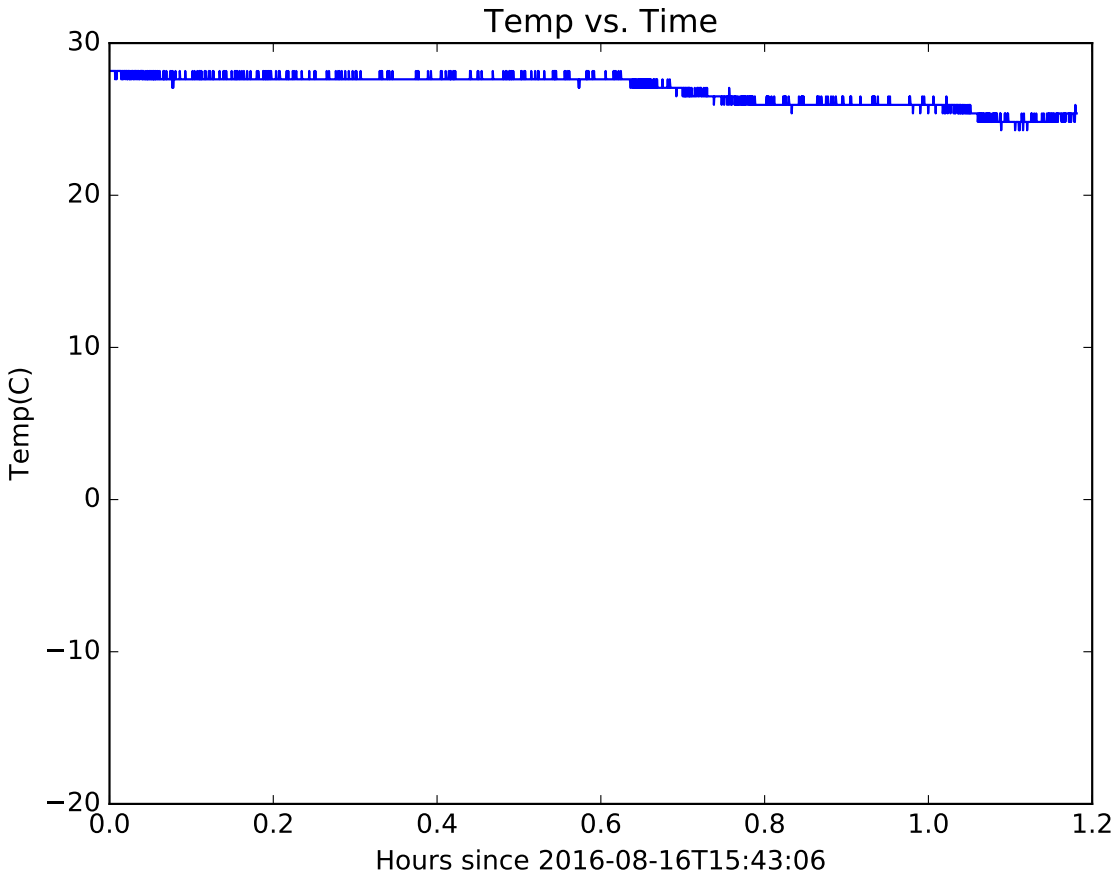
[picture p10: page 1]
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

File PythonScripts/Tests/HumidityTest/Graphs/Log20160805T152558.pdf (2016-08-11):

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

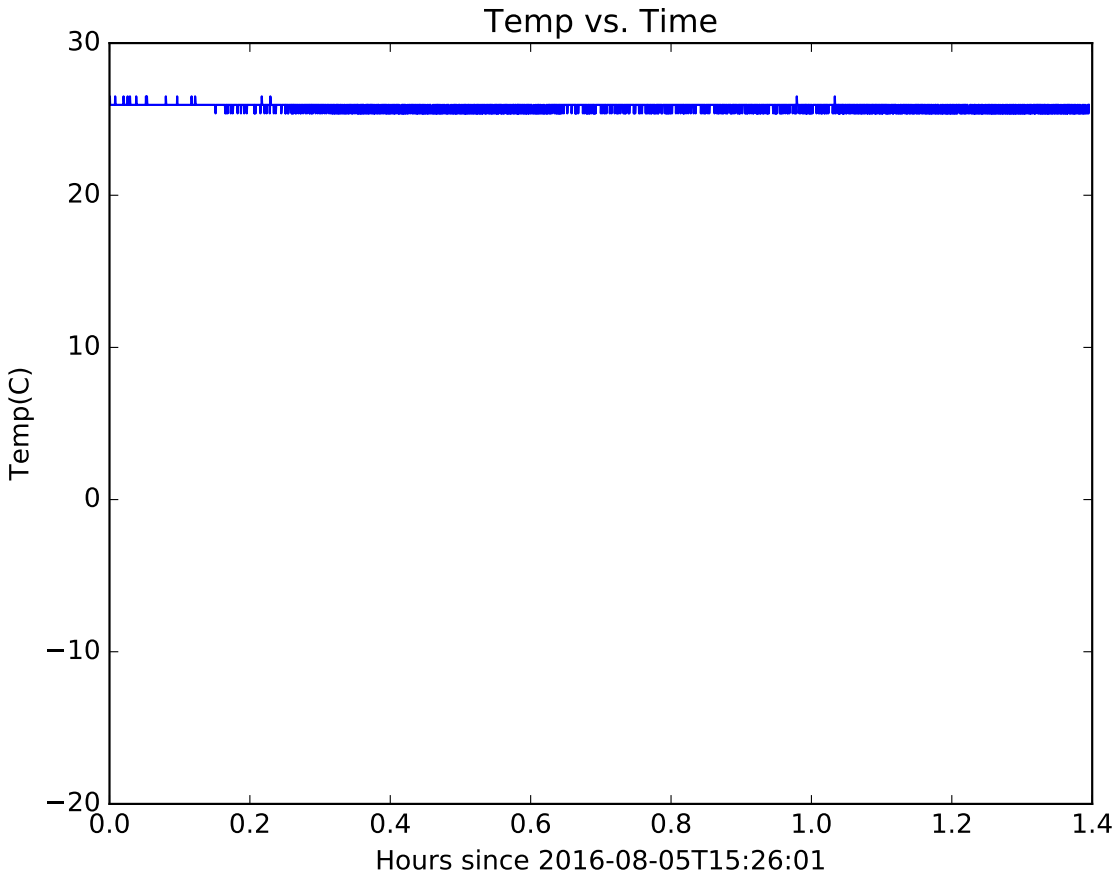
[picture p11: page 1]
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

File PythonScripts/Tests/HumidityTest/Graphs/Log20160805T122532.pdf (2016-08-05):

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

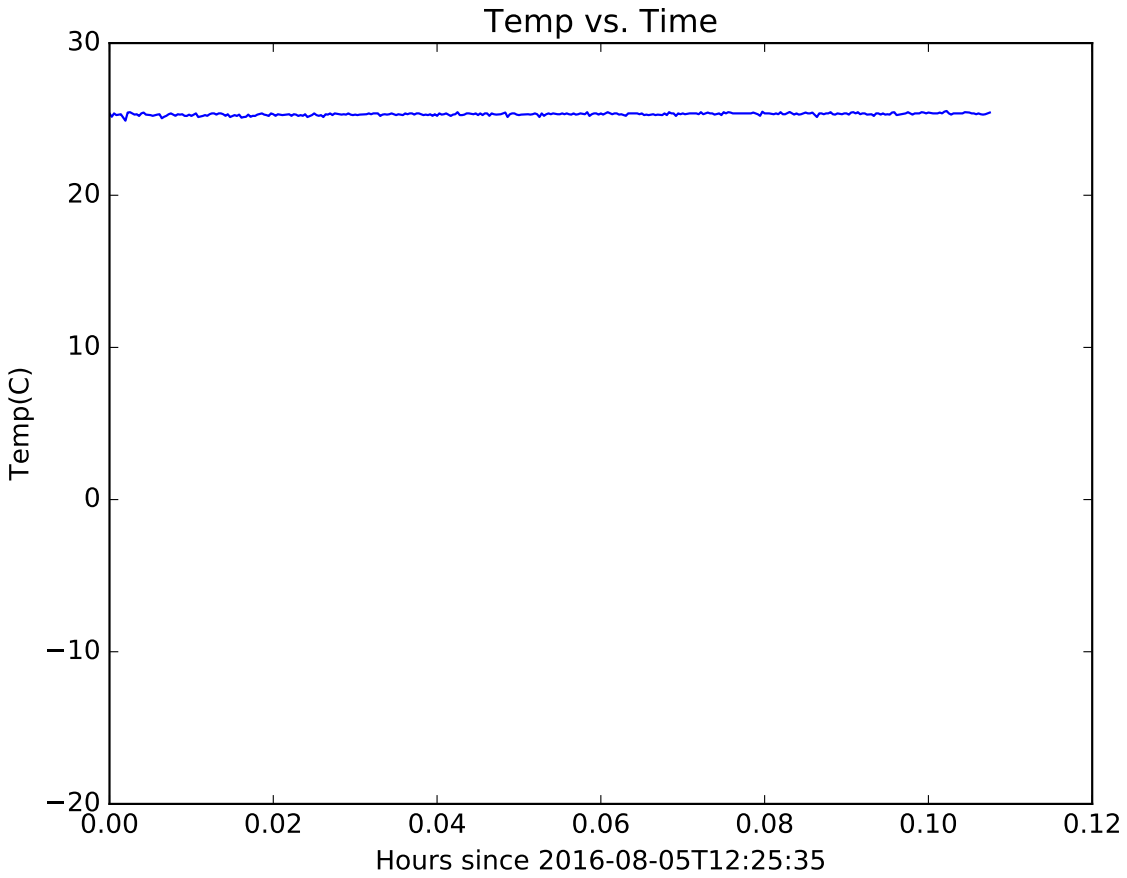
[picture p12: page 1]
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

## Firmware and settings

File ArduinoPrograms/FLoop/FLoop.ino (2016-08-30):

//PID stuff: Values for PID calculation
//PID is not being currently used and may not be used in the final product
int targetTemp = -10; 
double Actual = 0; 
double Error = 0;
double Integral = 0;
double Last = 0;
int IntThresh = targetTemp + 12;
double kP = 20;   
double kI = 0.1; 
double kD = 0.6; 
double ScaleFactor = 1;
int drive = 0; //Current drive value is 0, so no PID is used. If using PID, comment this line out
//Average calculation variables.
//Len 10 means over 1 second
const int len = 10; 
double prevTemps[len]; 
double averageTemp;
//If there are enough "outliers"/"bad readings", maybe they are actually correct. 
//If there are enough consecutive bad readings, then trust them.
int badReadings = 0;                   
int peltPin = 3;   //peltier cooler pin (smaller peltier touching board)
int peltPin1 = 9; //second peliter cooler pin (big peltier touching heatsink)
//
int outV = 12; 
double psuV = 12; 
//
float c;
//mechanism to turn peltiers off if the temp gets too hot (e.g. fan turns off or some failure)
int changeCount = 0;          //make sure at least 30 readings before switching states
double onThresh = -8;        //temperature threshold to turn on this mechanism. (on state)
double badThresh = 0;       //temperature threshold to signal that something bad is happening(bad state)
boolean reachedOn = false; //signals on state
int LEDPin = 10;          //LED that turns on during on state. Off signals a problem.
//Code to slowly ramp the MOSFET's on
  boolean MosfetsOn = false;
//
void setup() {
  pinMode(peltPin, OUTPUT); 
  pinMode(peltPin1, OUTPUT);
  Serial.begin(9600); 
  analogReference(INTERNAL); 
  pinMode(A0, INPUT_PULLUP); 
  pinMode(A1, OUTPUT); 
  pinMode(LEDPin, OUTPUT); 
  digitalWrite(A1, LOW); 
  digitalWrite(LEDPin, LOW);
  Last = readTemperature(); 

  //fills temperature array for initial average calculation
  double temp = readTemperature(); 
  for(int i = 0; i < len; i++)
    prevTemps[i] = temp;
}

void loop() { 
  double currentTemp = readTemperature(); 
  double ave = getAve(); 
  
  if(badReading(currentTemp)) 
    currentTemp = getAve();                   //using average if current reading is "outlier"
  else
    recordTemp(currentTemp);                            
    
  //*Uncomment below part to do PID stuff
  //int drive = getPID();                   //calculates what drive value (out of 255) to use for PWM. Proportional to duty cycle (i.e. 51/255 = 0.2, meaning 20% duty cycle)
  //analogWrite(peltPin, drive);            //writes drive value to small Peltier
  //analogWrite(peltPin1, drive);           //writes drive value to large Peltier


  //Slowly ramps up the Mosfet's (to max power in ~30 seconds).
  //Receives and sends messages to Python
  String inMsg = Serial.readString();
  if(inMsg == "Mosfets_On"){
    MosfetsOn = HIGH;
  }
  if(inMsg == "Mosfets_Off"){
    digitalWrite(LEDPin, LOW);
    for(int i = 0; i < 3; i++)
      Serial.println("Fets_Off"); //Tell the python that the message was received (and Mosfet's have been turned off)
    MosfetsOn = LOW;
    drive = 0;  //currently using drive to slowly ramp up V to Peltier's
  }
  if(MosfetsOn){
    digitalWrite(LEDPin, HIGH);
    drive = constrain(drive + 1, 0, 255); //currently using drive to slowly ramp up V to Peltier's
  }  
  //OutputVoltage(outV, psuV, peltPin);       // smaller & orange (max 14.4V and 6.4A). TEC1-12706
  analogWrite(peltPin, drive);              //currently using drive to slowly ramp up V to Peltier's
  analogWrite(peltPin1, drive); 
  
  checkSafe(ave);                           //Checking safety mechanism

  Serial.print(currentTemp); //prints the target temp. This is what the python script cares about


  
  //The python script ignores all of this.
  double raw = analogRead(A0); 
  Serial.print("    Raw: ");
  Serial.print(raw); 
  
  Serial.print("    T: ");
  Serial.print(currentTemp); 
  
  Serial.print("    Tf: ");
  Serial.print(getF(currentTemp)); 
  
  Serial.print("   TAve: ");
  Serial.print(ave); 
  
  Serial.print("   Dr:");
  Serial.println(drive); 
  
  delay(100); 
}




/*FUNCTIONS:
 * checkSafe(ave); Safety mechanism to turn off Peltier's if system starts getting hot
 * getPid(); calculates PID value and returns it. Can be used like:  int drive = getPID(); 
 * badReading(temp); Checks whether temp is an outlier (e.g. bad diode reading) and returns the result
 * recordTemp(temp); Takes the parameter (temp) and stores it for average calculation. Can be used like:  recordTemp(currentTemp);
 * getAve(); Calculates the average. Can be used like: double average = getAve()
 * readTemperature(); Calculates temperature form raw input and returns it. Can be used like:  double currentTemp = readTemperature();
 * getF(C); Converts a celsius temperature into fahrenheit and returns it
 * OutputVoltage(v, SrcV, pin); Calculates duty cycle to use to reach v from the SrcV (source voltage) and outputs it to the pin. Can be used like: OutputVoltage(3, psuV, peltPin);
 */

void checkSafe(double ave){
  if(reachedOn == false && ave < onThresh)       //increase the counter to reach the on state
    changeCount +=1;
    
  if(changeCount >= 30 && reachedOn == false){  //if 30 counts met, turns the mechanism on (on state)
    changeCount = 0;
    reachedOn = true;
    //digitalWrite(LEDPin, HIGH);
  }

  if(reachedOn == true && ave >= badThresh)     //increase the counter to reach the "problem state". Must be in on state
    changeCount +=1;

  if(reachedOn == true && ave < badThresh)     //Makes it so the counts must be consecutive.
    changeCount = 0;
    
  if(changeCount >= 30 && reachedOn == true){  //if 30 counts met, the mechanism reports a problem and turns off the Peltiers
    changeCount = 0;
    outV = 0;
    for(int i = 0; i < 3; i++)                //Signaling Python to email
      Serial.println("failure");
    //digitalWrite(LEDPin, LOW);
  }
}

//function that calculates and returns PID value.  
int getPID(){ 
  Actual = readTemperature();
  Error = Actual - targetTemp;

  if(abs(Error)<IntThresh && abs(Last-Actual) < 4){   //prevents spikes
    Integral = Integral + Error;
  }
  else{
    Integral = 0;
  }
  
  double P = Error * kP;
  double I = Integral * kI;
  double D = (Last-Actual)*kD;
  double Drive = P+I+D;
  Last = Actual;
  Serial.print("P: ");
  Serial.print(P);
  Serial.print("    I:");
  Serial.print(I);
  Serial.print("    D:");
  Serial.print(D);
  Serial.print("    ");
  Drive = Drive*ScaleFactor;
  if(Drive>255){
    Drive = 255;
  }
  if(Drive<0){
    Drive = 0;
  }
  return Drive;
}

//To ignore spikes or misreadings, this will only allow readings 3 degrees from the average
//If there are enough bad readings, they might actually be right. 
//If # of badReadings high enough, will now trust these "bad" readings
boolean badReading(double temp){
  double ave = getAve();
  if(abs(temp-ave) >=3 && badReadings < 5){
    badReadings++;
    return true;
  }
  else{
    badReadings = 0;  
    return false;
  }
}

//records temperature for calculating average
void recordTemp(double temp){ 
  for(int i = len-1; i > 0 ; i--){
    prevTemps[i] = prevTemps[i-1];
  }
  prevTemps[0] = temp;
}

//calculates and returns average
double getAve(){ 
  double sum = 0;
  for(int i = 0; i < len; i++)
    sum += prevTemps[i];
  return (double)(sum / len); 
}

//calculates and returns temperature. 
double readTemperature(){ 
  double in = analogRead(A0); 
  c = (-0.5584*in) + 357.63;
  return c;
}

//converts C to F
double getF(double C){ 
  return (9*(C/5) + 32);
}

//uses PWM to output voltage using calculated duty cycle. Ex: v = 2.4, SrcV = 12. Uses a 20% duty cycle
void OutputVoltage(double v, double SrcV, int pin) { 
  analogWrite(pin, (v / SrcV) * 255);
}

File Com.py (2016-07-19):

#Useful Forum- http://forum.arduino.cc/index.php?topic=92457.0
#http://goo.gl/urER4U
import time
import io
import serial.tools.list_ports
import serial
import signal # For trapping ctrl-c or SIGINT
import sys # For exiting program with exit code
import csv
#import smtplib 

temps = ()

def SIGINT_handler(signal, frame):
        print('Quitting program!')
        ser.close()
        sys.exit(0)
def getTemp(msg):
    for i in range(len(msg)): #the instantaneous temperature is the first "word"
        if(msg[i:i+1] == " "):
            return msg[0:i]
    return -1
 
def recordTemp(temp):
    global temps
    temps = temps + (float(temp),) 
    
def resetTemps():
    global temps
    temps = ()
    
def getTempAve(): #Average over the out_Period
    global temps
    sum = 0
    for i in temps:
        sum += i
    return (sum / len(temps))

signal.signal(signal.SIGINT, SIGINT_handler)

port_names=[]
a=serial.tools.list_ports.comports()
for w in a:
    port_names.append(w.device)
 
port_names.sort()
print('\nDetected the following serial ports:\nDon\'t choose /dev/ttyAMA0.')
i=0
for w in port_names:
    print('%d) %s' %(i,w))
    i=i+1
total_ports=i # now i= total ports

user_port_selection=input('\nSelect port: (0,1,2...)    ')
if (int(user_port_selection)>=total_ports):
    exit(1) # port selection out of range

out_period = 0
while(out_period <0.1): 
    out_period = input('Output data how often(seconds)? Minimum 0.1s    ')

ser=serial.Serial(port=port_names[int(user_port_selection)],baudrate=9600,timeout=1)
    
def syncToBoard():
    mycmd = ""
    while(mycmd != "\n"):
        mycmd=ser.read()

start = time.time()
syncToBoard()
while(1):
    msg = ""
    mycmd = ""
    while(mycmd != "\n"):
        msg += mycmd
        mycmd=ser.read()
    
    
    global start
    if(len(msg)>0):
        now= time.strftime("%Y-%m-%dT%H:%M:%S") #ISO 8601 time format
        msg = getTemp(msg)
        #print msg
        recordTemp(msg)
        dt = time.time() - start
        if(dt >= out_period):
            start = time.time()
            msg = getTempAve()
            resetTemps()
            #print dt
            with open("Log.txt", "a") as f:
	       f.write("%s    %s\n" %(now, msg))
	    #with open('Log.csv', 'a') as csvfile:
 	    #   writer = csv.writer(csvfile)
	    #   writer.writerow([now, str(msg)])
            print ("%s    %s" %(now, msg))

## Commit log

2016-06-20 Sample for feedback loop system
2016-06-22 Testing dual mosfets and diode "thermometer"
2016-06-22 Converted input into temperature
2016-06-23 Added diode temperature reading
2016-06-23 Calibrated diode temperature sensing
2016-06-27 Implemented PID
    coefficients need calibration
2016-07-11 Updated Peltier Output Pin
2016-07-11 Updated temperature equation
2016-07-12 More accurate temperature equation
2016-07-18 Added python communication and timestamps
    [Circuit.fzz]
2016-07-19 Fixed startup crash error
    [Com.py]
2016-07-19 Switched output from txt to csv
    [Log.csv]
2016-07-20 Added timestamps to log file names
    [Log20160720T113154.csv]
2016-07-20 Sends email alerts for failures
    [Log.csv, Log20160720T134028.csv, Log20160720T135216.csv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]
2016-07-21 Commented programs and created a readme
    [Log20160720T113154.csv, Log20160720T134028.csv, Log20160720T135216.csv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]
2016-07-21 Fixed a quick grammatical mistake
    [Com.py]
2016-07-21 Fixed and cleaned up parts of schematic
    [Circuit.fzz]
2016-07-21 Uses matplotlib to realtime plot
    [Log20160720T154955(SecondOvernight).csv, Log20160721T161451.csv, Log20160721T161533.csv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]
2016-07-21 Quick fix for log writing error
    [Log20160721T164447.csv]
2016-07-22 Updated schematic
    [Circuit.fzz, Log20160721T165038.csv, Log20160721T165252.csv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]
2016-07-25 Switched from matplotlib to pyqtgraph
    pyqtgraph is significantly faster for graphing real-time data and will
    be more useful
    [Log20160725T100846.csv, Log20160725T101145.csv, Log20160725T101909.csv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]
2016-07-26 Ran first nitrogen test
    [FirstNitrogenTest.csv, Log20160725T180803.csv, Log20160726T110440.csv]
2016-07-26 Added grids for graph
    [Log20160726T142310.csv, Log20160726T144159.csv]
2016-07-27 Completed FileWriter class
    [Log20160727T143744.csv]
2016-07-27 Completed Emailer class
    [Log20160727T144921.csv, Log20160727T145448.csv, Log20160727T145756.csv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]
2016-07-27 Completed Grapher class
    [Log20160727T155022.csv, Log20160727T155134.csv, Log20160727T155402.csv]
2016-07-27 Added pdf of schematic
    [Circuit.fzz]
2016-07-28 Made comments more moderate
    comments were too heavy
    [Log20160728T101814.csv, Log20160728T102622.csv, Log20160728T122620.csv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]
2016-07-28 Inverted graph colors
    [Log20160728T132949.csv, Log20160728T133017.csv, Log20160728T133054.csv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]
2016-07-28 Added batch file to run python
    [Log20160728T133747.csv, Log20160728T134006.csv, Log20160728T134520.csv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]
2016-07-28 Changed how LED works
2016-08-02 Fixed GUI unresponsiveness
    calls app.processEvents() every tick now
    [ActualNitrogenTest1.csv, ActualNitrogenTest2.csv, Log20160801T102534.csv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]
2016-08-02 Saves PDF in graphs folder with appropriate name
    [Log20160802T112538.csv]
2016-08-02 Com produces pdf graph during exit
    [Log20160802T142411.csv, Log20160802T142816.csv, Log20160802T142849.csv]
2016-08-04 Added humidity sensor test
    [Log20160802T171806.csv]
2016-08-05 Humidity test calculates and prints humidity averages
    [Log20160805T114423.csv, Log20160805T115239.csv, Log20160805T115404.csv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]
2016-08-05 Added second sensor
    This sensor records the humidity and temperature outside of the
    styrofoam box. Uses the Temp_Handler object to store the data. This is
    somewhat ad-hoc as it uses functions meant for the temperature on the
    humidity.
    [Log20160805T122532.csv, Log20160805T123205.csv, Log20160805T150226.csv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]
2016-08-11 Updated email list and temporarily changed thresholds for irradiated Peltier
    [Log20160805T152558.csv, Log20160811T164927(FirstIrradiatedTest).csv, Log20160811T164927.csv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]
2016-08-12 Tested irradiated Peltier
    [Log20160811T171401(FirstOvernightIrradiatedTest).csv, Log20160811T171401.csv, Log20160812T103658.csv]
2016-08-15 Tested irradiated Peltier again
    [Log20160812T103658(IrradiatedComparisonTest).csv, Log20160815T104545(NormalComparison2).csv, Log20160815T104545.csv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]
2016-08-16 Tested the air blower
    [Log20160815T144156.csv, Log20160815T154143.csv, Log20160816T124842.csv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]
2016-08-16 FileWriterH now writes all data to CSV
    [Log20160816T151800.csv, Log20160816T152124.csv]
2016-08-17 Tested air supply overnight
    [Log20160816T153712.csv, Log20160816T154303.csv, Log20160816T165631(FirstBlowerOvernightTest).csv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]
2016-08-17 Tested single Peltier alone
    [Log20160817T141711(LoneTec12706Test).csv, Log20160817T141711.csv, Log20160817T155423.csv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]
2016-08-18 Tested many Peltier setups
    [Log20160817T164839.csv, Log20160817T164921.csv, Log20160817T165312.csv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]
2016-08-19 Uploaded graphs used to calibrate diode
    [DiodeTemperatureGraphs.xlsx]
2016-08-19 Changed some values
    [DiodeTemperatureGraphs.xlsx]
2016-08-30 Updated testing emails
    [Log20160830T105627.csv]
2016-08-30 Serial output from python works and tested
    [Log20160830T110021.csv, Log20160830T110426.csv, Log20160830T110918.csv]
2016-08-30 Gave meaning to python outputs
    [Log20160830T111335.csv, Log20160830T111439.csv, Log20160830T111552.csv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]
2016-08-30 Mosfet ramping almost works
    [Log20160830T113312.csv, Log20160830T113405.csv, Log20160830T113814.csv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]
2016-08-30 Mosfet ramping programmed but not tested
    [Log20160830T120847.csv, Log20160830T121147.csv, Log20160830T121657.csv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]
